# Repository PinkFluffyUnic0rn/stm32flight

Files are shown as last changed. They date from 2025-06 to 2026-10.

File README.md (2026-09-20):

STM32 Flight controller
=========================

DIY quadcopter flight controller from scratch, two boards and software.

[Project structure](https://github.com/PinkFluffyUnic0rn/stm32flight/wiki/Project-structure) 
is described on wiki page.

Software
=======

Software part implements all basic quadcopter flight control features.
Configuration commands and settings are on
[wiki page](https://github.com/PinkFluffyUnic0rn/stm32flight/wiki/FC-configuration-commands-and-settings).

* Rotation speed stabilization using gyroscope readings.
* Attitude stabilization using accelerometer/gyroscope readings.
* Yaw stabilization using gyroscope readings.
* Yaw stabilization using magnetometer/gyroscope readings.
* Acceleration stabilization using accelerometer readings.
* Altitude stabilization using barometer/accelerometer readings.
* Position stabilization using GNSS/accelerometer/magnetometer readings.
* Configuration through Wi-Fi.
* Dshot-300 and Dshot-600 ESC control protocols.
* IRC Tramp VTX control.
* OSD for digital VTX through MSP.
* Telemetry and control through eLRS.
* Terminal configuration tool.
* Qt5 based GUI configuration tool for desktop and android.

STM32H723 based board
=======
[Schematic](https://github.com/PinkFluffyUnic0rn/stm32flight/blob/main/pcb/H7/schematic.pdf)

 * MCU: STM32H723VGT6
 * Crystall oscillator: 20 Mhz
 * DC-DC converter for control board: TPS5430
 * Control board voltage regulator: LDL1117S33R
 * Accelerometer/Gyroscope: ICM-42688-P
 * Barometer: DPS368
 * Magnetometer: LIS3MDL
 * External magnetometer: MMC5983MA
 * Flight log storage: W25Q
 * GNSS module: M10
 * Remote control: ERLS CRSF receiver
 * Telemetry/debug/config: ESP8285

STM32F405 based board
=======
 * MCU: STM32F405RGT6
 * Crystall oscillator: 20 Mhz
 * DC-DC converter for control board: TPS5430 (external)
 * Control board voltage regulator: LDL1117S33R-3.3
 * Accelerometer/Gyroscope: ICM-42688-P
 * Barometer: DPS368
 * Magnetometer: QMC5883L
 * Flight log storage: W25Q
 * GNSS module: M10
 * Remote control: ERLS CRSF receiver
 * Telemetry/debug/config: ESP8285

The quadcopter used for testing
==========
 * Motors: 1404, 3800 kV
 * Props: 3030
 * Battery: 14.8v (4s), 1300 mAh, 120c
 * Frame: carbon fiber
 * Canopy, VTX mount: 3d printed PLA
 * Landing pads: EVA foam

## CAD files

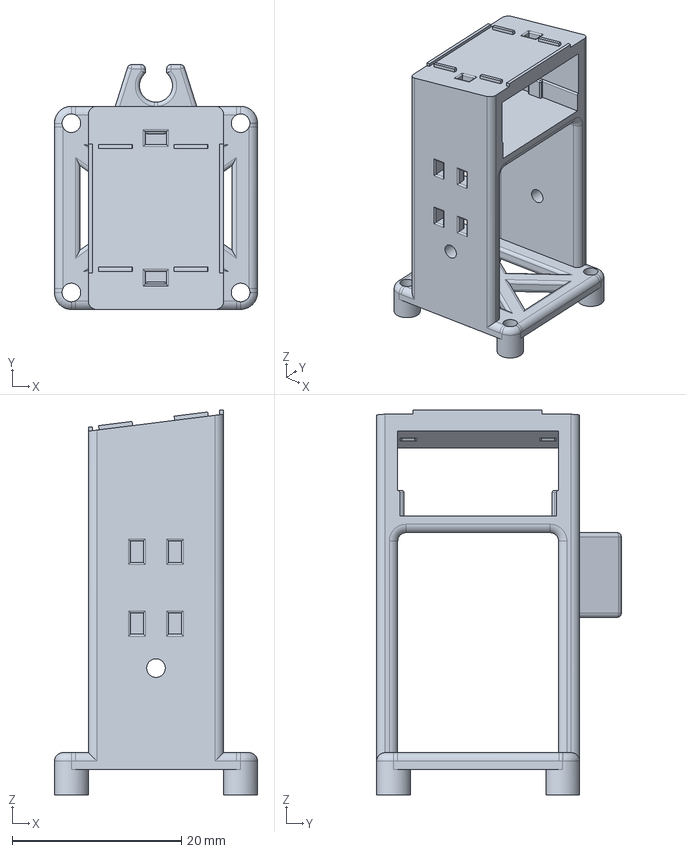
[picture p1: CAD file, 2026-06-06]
cad/canopy.FCStd
24.0 x 28.9 x 45.5 mm

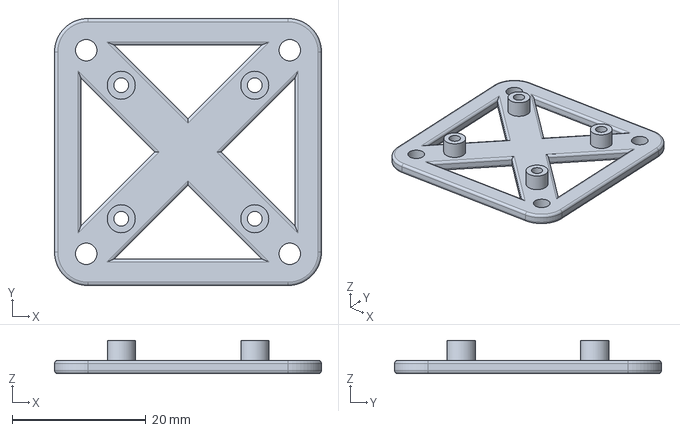
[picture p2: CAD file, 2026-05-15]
cad/vtx_mount.FCStd
40.0 x 40.0 x 5.00 mm

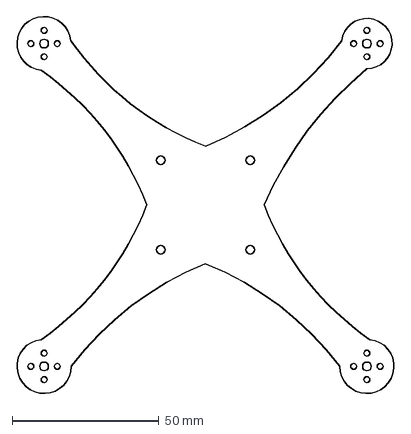
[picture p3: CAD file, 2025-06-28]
cad/frame.dxf
129.1 x 128.8 mm

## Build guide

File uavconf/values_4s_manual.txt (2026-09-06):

adj acc x 0
adj acc y 0
adj acc z 0
adj acc xtscale 0
adj acc ytscale 0
adj acc ztscale 0.00058
adj althold coefa 3.484
adj althold coefb 0
adj althold coefc 0.15
adj althold hover 0.287
adj althold tiltcoefmax 0.25
adj pitch 0.01
adj roll 0
adj yaw 0
adj bat scale 1
adj curr offset -17
adj curr scale 412.5
adj gyro x 1.445184
adj gyro y 0.595486
adj gyro z 0.414855
adj mag x0 0.173815
adj mag y0 -0.076065
adj mag z0 -0.041577
adj mag decl 0.322
adj mag xscale 0.960479
adj mag yscale 0.957427
adj mag zscale 1
adj mag xthscale 0
adj mag ythscale 0
adj mag zthscale 0
adj pitchthrust 0
adj rollthrust 0
adj thrust 1.6
ctrl accel 0.5
ctrl altmax 4
ctrl pitch 0.25
ctrl roll 0.25
ctrl thrust 0.9
ctrl climbrate 1.5
ctrl spitch 1
ctrl spos 2
ctrl sroll 1
ctrl sspeed 4
ctrl syaw 1.5
irc frequency 5865
irc power 25
compl altitude 1
compl attitude 1
compl climbrate 1
compl pos 1
compl speed 1
compl yaw 1
feature matrixatt 1
feature notchen 0
lpf vaccel 1
lpf accel 100
lpf d 100
lpf gyro 100
lpf mag 50
notch gyrovbat 17
notch gyrofrmax 2038
notch gyrofrmin 220
log freq 128
log recsize 8
log record 0 none
log record 1 none
log record 10 none
log record 2 none
log record 3 none
log record 4 none
log record 5 none
log record 6 none
log record 7 none
log record 8 none
log record 9 none
log record 11 none
log record 12 none
log record 13 none
log record 14 none
log record 15 none
log record 16 none
log record 17 none
log record 18 none
log record 19 none
log record 20 none
log record 21 none
log record 22 none
log record 23 none
log record 24 none
log record 25 none
log record 26 none
log record 27 none
log record 28 none
log record 29 none
log record 30 none
log record 31 none
motor lb 1
motor lt 0
motor rb 3
motor rt 2
pid altitude d 0
pid altitude i 0
pid altitude p 1.7
pid tilt d 0
pid tilt i 0
pid tilt p 9
pid climbrate d 0
pid climbrate i 0
pid climbrate p 0.6
pid feature altclamp 1.5
pid feature attimax 0.1
pid feature thrimax 0.1
pid feature iscaling 0.51
pid feature yawclamp 0.125
pid stilt d 0.001667
pid stilt i 8.640009
pid stilt p 0.24
pid throttle d 0
pid throttle i 3
pid throttle p 3
pid syaw d 0
pid syaw i 0
pid syaw p 1.5
pid yaw d 0
pid yaw i 0
pid yaw p 1.5
pid pos d 0
pid pos i 0
pid pos p 1
pid speed d 0
pid speed i 0
pid speed p 5

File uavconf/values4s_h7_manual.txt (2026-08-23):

adj acc x 0
adj acc y 0
adj acc z 0
adj acc xtscale 0
adj acc ytscale 0
adj acc ztscale 0.00058
adj althold coefa 0
adj althold coefb 0
adj althold coefc 0
adj althold hover 0.64
adj althold tiltcoefmax 0.25
adj pitch 0.01
adj roll 0
adj yaw 0
adj bat scale 1
adj curr offset -17
adj curr scale 412.5
adj gyro x 0.945184
adj gyro y 0.795486
adj gyro z 0.414855
adj mag x0 0.077877
adj mag y0 -0.055068
adj mag z0 0.047812
adj mag decl 0.322
adj mag xscale 0.965043
adj mag yscale 0.975738
adj mag zscale 1
adj mag xthscale 0
adj mag ythscale 0
adj mag zthscale 0
adj pitchthrust 0
adj rollthrust 0
adj thrust 1.6
ctrl accel 0.5
ctrl altmax 4
ctrl pitch 0.25
ctrl roll 0.25
ctrl thrust 0.9
ctrl climbrate 1.5
ctrl spitch 1
ctrl spos 2
ctrl sroll 1
ctrl sspeed 4
ctrl syaw 1.5
irc frequency 5865
irc power 25
compl altitude 1
compl attitude 5
compl climbrate 1
compl pos 1
compl speed 1
compl yaw 1
feature matrixatt 1
feature notchen 0
lpf vaccel 0.636
lpf accel 100
lpf d 100
lpf gyro 100
lpf mag 15
notch gyrovbat 7.2
notch gyrofrmax 358
notch gyrofrmin 170
log freq 4000
log recsize 8
log record 0 none
log record 1 none
log record 10 none
log record 2 none
log record 3 none
log record 4 none
log record 5 none
log record 6 none
log record 7 none
log record 8 none
log record 9 none
log record 11 none
log record 12 none
log record 13 none
log record 14 none
log record 15 none
log record 16 none
log record 17 none
log record 18 none
log record 19 none
log record 20 none
log record 21 none
log record 22 none
log record 23 none
log record 24 none
log record 25 none
log record 26 none
log record 27 none
log record 28 none
log record 29 none
log record 30 none
log record 31 none
motor lb 1
motor lt 0
motor rb 3
motor rt 2
pid altitude d 0
pid altitude i 0
pid altitude p 1.7
pid tilt d 0
pid tilt i 0
pid tilt p 9
pid climbrate d 0
pid climbrate i 0
pid climbrate p 0.6
pid feature attimax 0.1
pid feature thrimax 0.1
pid feature iscaling 0.51
pid stilt d 0.003333
pid stilt i 17.280017
pid stilt p 0.48
pid throttle d 0
pid throttle i 6.5
pid throttle p 6.5
pid syaw d 0
pid syaw i 0
pid syaw p 3
pid yaw d 0
pid yaw i 0
pid yaw p 1.5
pid pos d 0
pid pos i 0
pid pos p 0.1
pid speed d 0
pid speed i 0
pid speed p 0.1

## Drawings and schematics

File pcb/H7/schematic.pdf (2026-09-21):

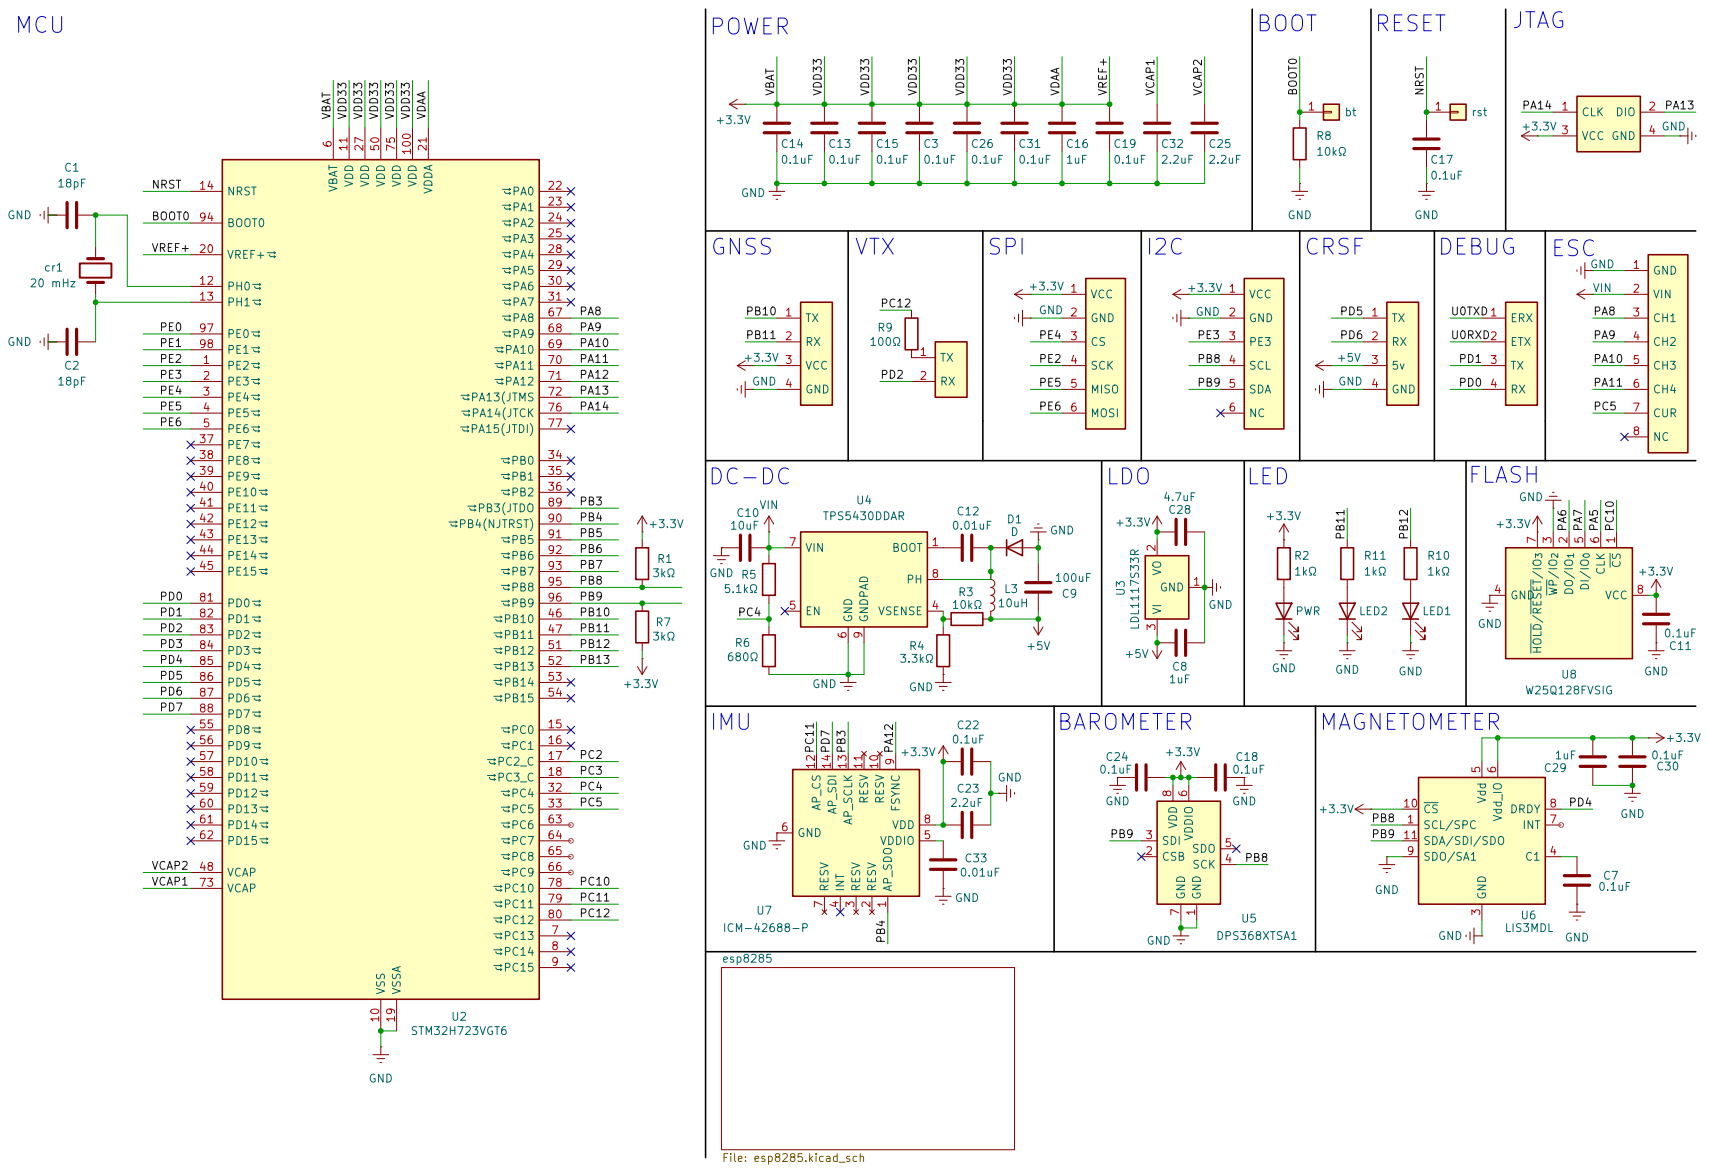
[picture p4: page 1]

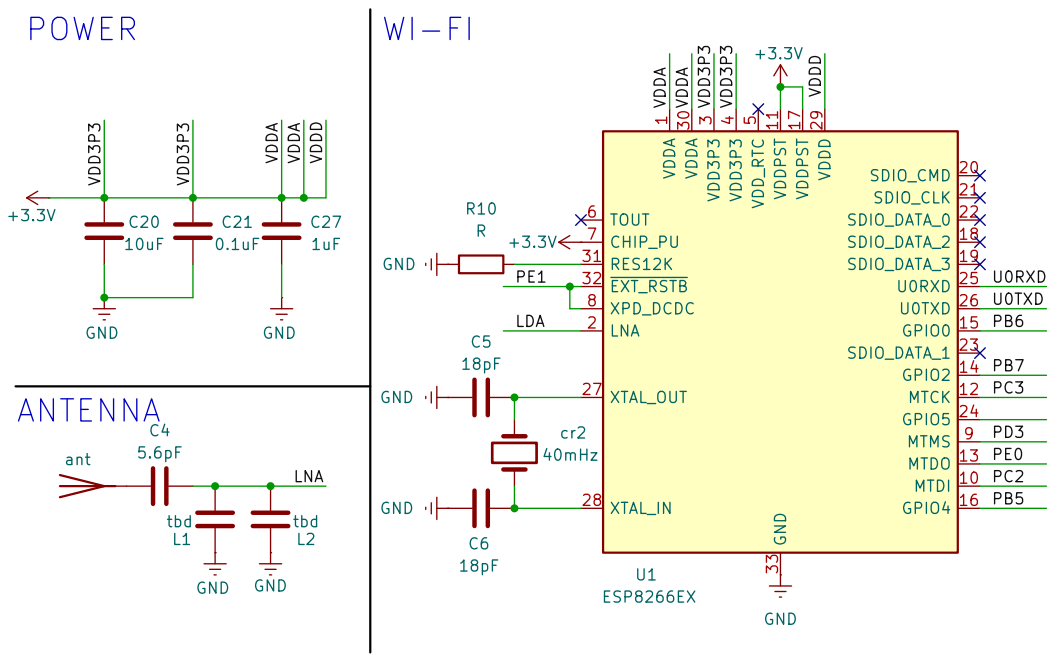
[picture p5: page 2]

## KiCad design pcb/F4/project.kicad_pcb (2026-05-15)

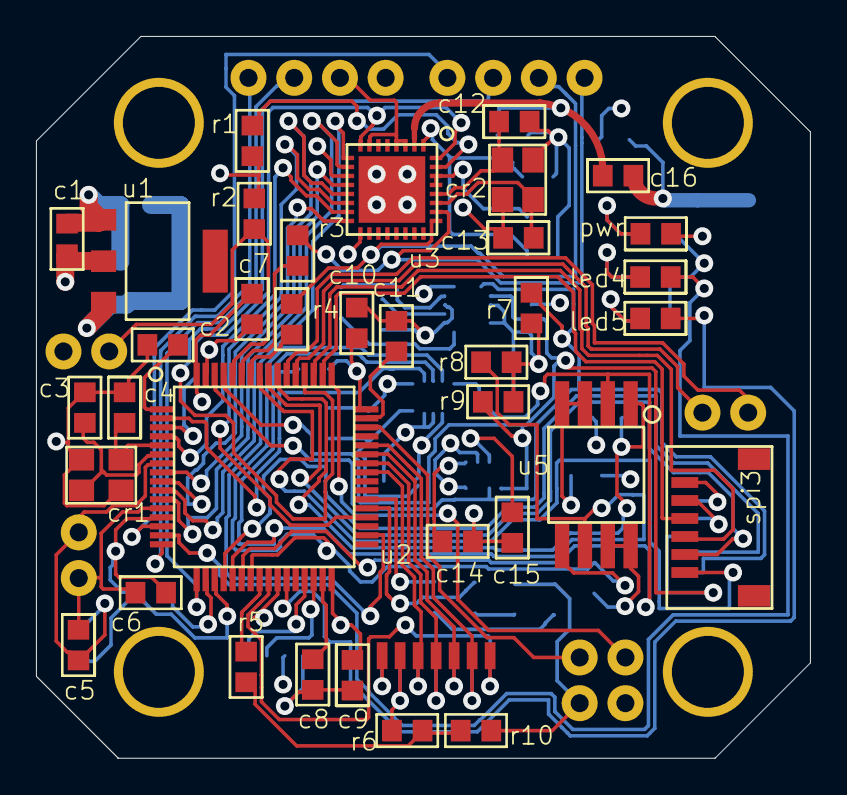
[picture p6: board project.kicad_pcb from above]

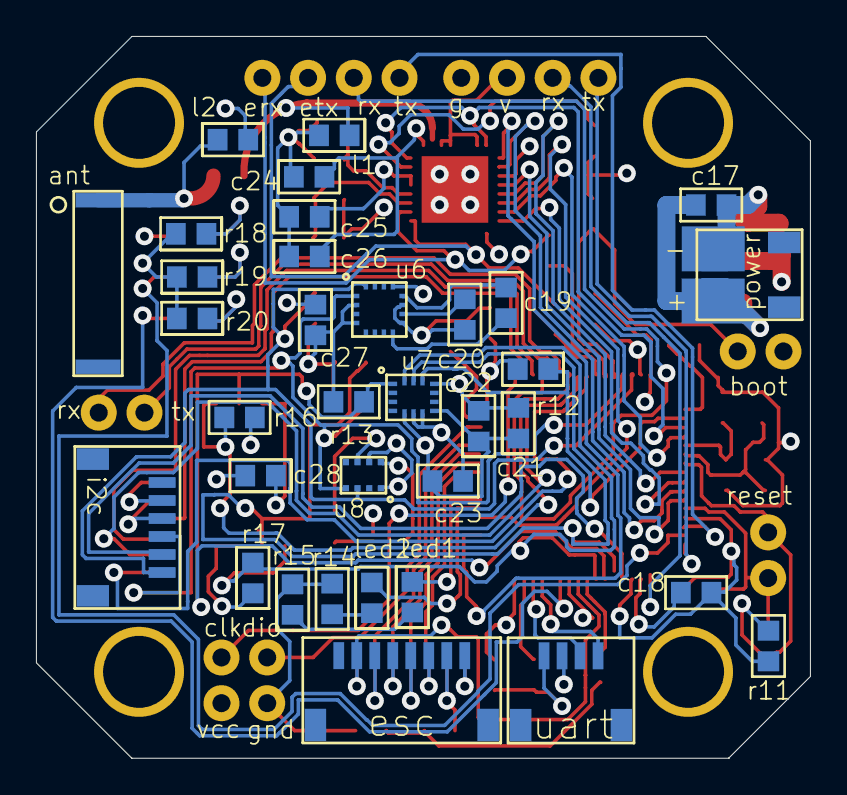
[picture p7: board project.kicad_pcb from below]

Board: 4 copper layers, 43.0 x 40.1 mm, 70 parts (34 on the bottom side), 45 nets.

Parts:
ant: Comment; rainsun antenna
c1: Comment; PCBComponent_1
c2, c3, c4, c5, c6, c7, c8, c9, c10, c11, c12, c13, c14, c15, c16, c17, c18, c19, c20, c21, c22, c23, c24, c25, c26, c27, c28: Comment; 0603
cr1, cr2: Comment; smd_crystall
esc: Comment; SH1.0-8
i2c: Comment; SH1.0-6
l1, l2: Comment; 0603
led1, led2, led4, led5: Comment; 0603
power: Comment; sh1.0-2
pwr: Comment; 0603
r1, r2, r3, r4, r5, r6, r7, r8, r9, r10, r11, r12, r13, r14, r15, r16, r17, r18, r19, r20: Comment; 0603
spi3: Comment; SH1.0-6
u1: Comment; ams1117
u2: Comment; lqfp64
u3: Comment; esp8285
u5: Comment; w25q
u6: Comment; qmc5883l
u7: Comment; icm42688
u8: Comment; DPS368
uart: Comment; sh1.0-4

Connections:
ant: ant.6, c16.1, l2.1
antcap: c16.1, l1.1, u3.4
boot: r2.1, u2.1
ch1: esc.1, u2.1
ch2: esc.1, u2.1
ch3: esc.1, u2.1
ch4: esc.1, u2.1
ch5: spi3.1, u2.1
ch6: spi3.1, u2.1
cs1: r12.1, u2.1, u7.1
cs2: r16.1, u2.1, u5.1
cs4: u2.1, u3.4
current: esc.1, u2.1
esp_rx: r3.1, u3.4
esp_tx: r4.1, u3.4
espboot: u2.1, u3.4
ext_rstb: u2.1, u3.4
exti1: u2.1, u3.4
gnd: c1.1, c2.1, c3.1, c4.1, c5.1, c6.1, c7.1, c8.1, c9.1, c10.1, c11.1, c12.1, c13.1, c14.1, c15.1, c17.1, c18.1, c20.1, c21.1, c22.1, c23.1, c24.1, c25.1, c26.1, c27.1, c28.1, cr1.3, cr2.3, esc.1, i2c.1, l1.1, l2.1, power.1, r1.1, r2.1, r10.1, r14.1, r15.1, r18.1, r19.1, r20.1, spi3.1, u1.1, u2.1, u5.1, u6.1, u7.1, u8.1, uart.1
led1: led2.1, u2.1
led1r: led2.1, r14.1
led2: led1.1, u2.1
led2r: led1.1, r15.1
led3r: pwr.1, r18.1
led4: led4.1, u2.1
led4r: led4.1, r19.1
led5: led5.1, u2.1
led5r: led5.1, r20.1
miso: r13.1, u2.1, u5.1, u7.1
miso2: u2.1, u3.4
mosi: r17.1, u2.1, u5.1, u7.1
mosi2: u2.1, u3.4
nrst: c5.1, r11.1, u2.1
osc_in: c4.1, cr1.3, u2.1
osc_out: c3.1, cr1.3, u2.1
pa4: i2c.1, u2.1
pa15: spi3.1, u2.1
pb15: u2.1, u3.4
pc10: spi3.1, u2.1
qmc_c1: c20.1, u6.1
qmc_setc: c19.1, u6.1
qmc_setp: c19.1, u6.1
res12k: r1.1, u3.4
rx1: r3.1, u2.1
rx3: u2.1, uart.1
sck: r8.1, u2.1, u5.1, u7.1
sck2: u2.1, u3.4
scl: i2c.1, r9.1, u2.1, u6.1, u8.1
sda: i2c.1, r7.1, u2.1, u6.1, u8.1
tx1: r4.1, u2.1
tx3: u2.1, uart.1
v2_1: r5.1, r6.1, r10.1
v2_2: r5.1, u2.1
vbat: c2.1, u2.1
vcap1: c8.1, u2.1
vcap2: c11.1, u2.1
vcc: c1.1, c6.1, c7.1, c9.1, c10.1, c14.1, c15.1, c18.1, c21.1, c22.1, c23.1, c24.1, c25.1, c26.1, c27.1, c28.1, i2c.1, pwr.1, r7.1, r8.1, r9.1, r11.1, r12.1, r13.1, r16.1, r17.1, spi3.1, u1.1, u2.1, u3.4, u5.1, u6.1, u7.1, u8.1, uart.1
vesc: esc.1, r6.1
vin: c17.1, power.1, u1.1
xtal_in: c12.1, cr2.3, u3.4
xtal_out: c13.1, cr2.3, u3.4

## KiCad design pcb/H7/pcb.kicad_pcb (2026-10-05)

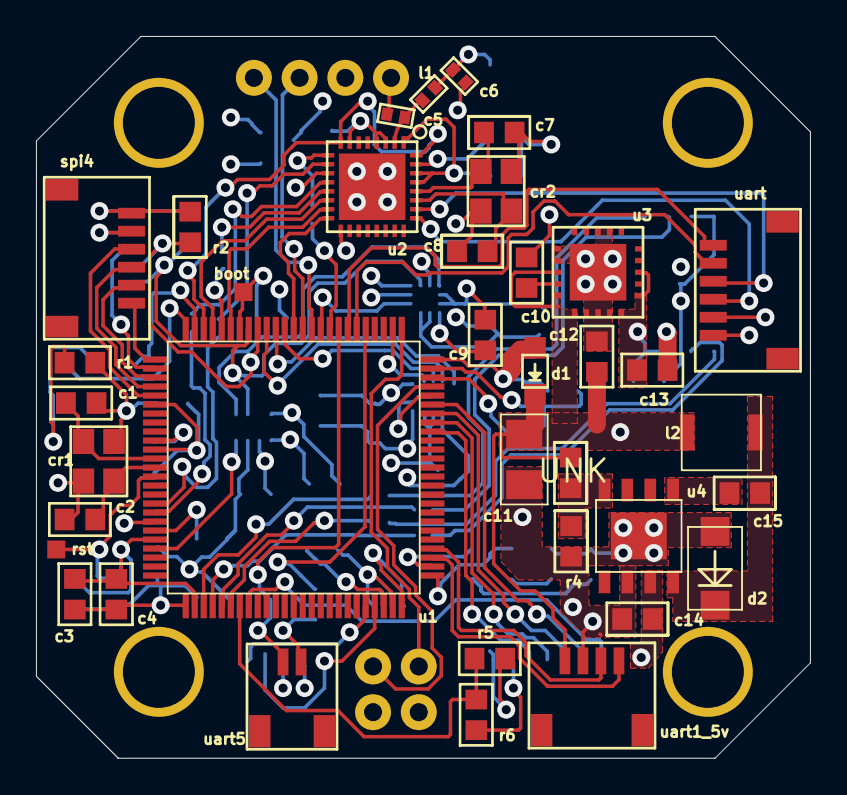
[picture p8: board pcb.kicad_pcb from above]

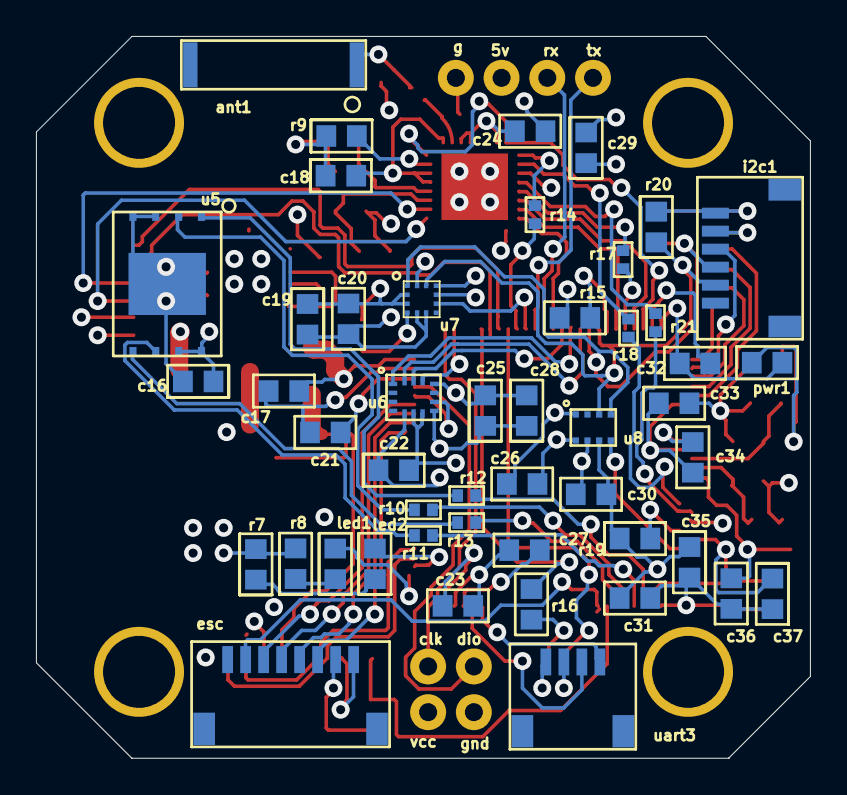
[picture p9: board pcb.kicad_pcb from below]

Board: 4 copper layers, 43.0 x 40.1 mm, 83 parts (48 on the bottom side), 59 nets.

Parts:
UNK: 10 kOhm; 0603
ant1: AN9520; rainsun antenna
c1, c2, c7, c8: 18 pF; 0603
c3, c10, c18, c20, c35: 1 uF; 0603
c4, c9, c16, c17, c19, c23, c24, c25, c26, c30, c31, c32, c33, c34, c36, c37: 0.1 uF; 0603
c5, c6: tbd; 0402
c11: 100 uF; 1206
c12, c14, c29: 10 uF; 0603
c13: 47 uF; 0603
c15, c22: 0.01 uF; 0603
c21, c27, c28: 2.2 uF; 0603
cr1: 20 Mhz; smd_crystall
cr2: 40 Mhz; smd_crystall
d1: Comment; SOD-323
d2: SS34
esc: JST SH-8; SH1.0-8
i2c1: JST SH-6; SH1.0-6
l1: tdb; 0402
l2: 10 uH; inductor
led1: blue LED; 0603
led2: orange LED; 0603
pwr1: green LED; 0603
r1, r7, r8: 1 kOhm; 0603
r2, r20: 3 kOhm; 0603
r4: 3.3 kOhm; 0603
r5: 680 Ohm; 0603
r6: 5.1 kOhm; 0603
r9: 12 kOhm; 0603
r10, r11, r12, r13, r14, r17, r18, r21: 33 Ohm; 0402
r15: 10 kOhm; 0603
r16: 100 Ohm; 0603
r19: 47 Ohm; 0603
spi4: JST SH-6; SH1.0-6
u1: STMH723VGT6; lqfp100
u2: ESP8285; esp8285
u3: TPS7A4700; TPS7A470
u4: TPS5430DDAR; tps5430
u5: Comment; W25N
u6: ICM-42688-P; icm42688
u7: LIS3MDLTR; lis3mdl
u8: DPS368XTSA1; DPS368
uart: JST SH-6; SH1.0-6
uart1_5v, uart3: JST SH-4; sh1.0-4
uart5: JST SH-2; sh1.0-2

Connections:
ant: ant1.6, c6.1, l1.1
antcap: c5.1, l1.1, u2.4
boot: r15.1, u1.1
ch1: esc.1, u1.1
ch2: esc.1, u1.1
ch3: esc.1, u1.1
ch4: esc.1, u1.1
current: esc.1, u1.1
dcdc_boot: c15.1, u4.9
drdy: u1.1, u7.6
esp_rx: u2.4, uart.1
esp_tx: u2.4, uart.1
espboot: u1.1, u2.4
ext_rstb: u1.1, u2.4
exti1: u1.1, u2.4
fsync: u1.1, u6.1
gnd: c1.1, c2.1, c3.1, c4.1, c5.1, c6.1, c7.1, c8.1, c9.1, c10.1, c11.10, c12.1, c13.1, c14.1, c16.1, c17.1, c18.1, c19.1, c20.1, c21.1, c22.1, c23.1, c24.1, c25.1, c26.1, c27.1, c28.1, c29.1, c30.1, c31.1, c32.1, c33.1, c34.1, c35.1, c36.1, c37.1, cr1.3, cr2.3, d2.8, esc.1, i2c1.1, r1.1, r4.1, r5.1, r7.1, r8.1, r9.1, r15.1, spi4.1, u1.1, u3.9, u3.10, u4.9, u5.11, u5.12, u6.1, u7.6, u8.1, uart.1, uart1_5v.1, uart3.1
led1: led1.1, u1.1
led1r: led1.1, r8.1
led2: led2.1, u1.1
led2r: led2.1, r7.1
lis_c1: c9.1, u7.6
loop: c15.1, d2.8, l2.7, u4.9
miso1_1: r10.1, u1.1
miso1_2: r10.1, u5.12
miso2_1: r18.1, u1.1
miso2_2: r18.1, u2.4
miso3: u1.1, u6.1
miso4: spi4.1, u1.1
mosi1_1: r13.1, u1.1
mosi1_2: r13.1, u5.12
mosi2_1: r21.1, u1.1
mosi2_2: r21.1, u2.4
mosi3: u1.1, u6.1
mosi4: spi4.1, u1.1
nr: c10.1, u3.9
nrst: c36.1, u1.1
nss1_1: r12.1, u1.1
nss1_2: r12.1, u5.12
nss2_1: r17.1, u1.1
nss2_2: r17.1, u2.4
nss3: u1.1, u6.1
nss4: spi4.1, u1.1
osc_in: c1.1, cr1.3, u1.1
osc_out: c2.1, cr1.3, u1.1
pe0: u1.1, u2.4
pe3: i2c1.1, u1.1
pwrled: pwr1.1, r1.1
res12k: r9.1, u2.4
rx1: u1.1, uart1_5v.1
rx3: u1.1, uart3.1
rx4: u1.1, uart.1
rx5: u1.1, uart5.1
sck1_1: r11.1, u1.1
sck1_2: r11.1, u5.12
sck2_1: r14.1, u1.1
sck2_2: r14.1, u2.4
sck3: u1.1, u6.1
sck4: spi4.1, u1.1
scl: i2c1.1, r2.1, u1.1, u7.6, u8.1
sda: i2c1.1, r20.1, u1.1, u7.6, u8.1
sdo: u1.1, u8.1
sence: UNK.1, r4.1, u4.9
tx1: u1.1, uart1_5v.1
tx3: u1.1, uart3.1
tx4: u1.1, uart.1
tx5_1: r16.1, u1.1
tx5_2: r16.1, uart5.1
v5: UNK.1, c11.10, c12.1, d1.4, l2.7, u3.9, uart1_5v.1
v_bat: r5.1, r6.1, u1.1
vcap1: c21.1, u1.1
vcap2: c27.1, u1.1
vcc: c3.1, c4.1, c13.1, c16.1, c17.1, c18.1, c19.1, c20.1, c22.1, c23.1, c24.1, c25.1, c26.1, c28.1, c29.1, c30.1, c31.1, c32.1, c33.1, c34.1, c35.1, c37.1, d1.4, i2c1.1, pwr1.1, r2.1, r19.1, r20.1, spi4.1, u1.1, u2.4, u3.9, u5.12, u6.1, u7.6, u8.1, uart.1, uart3.1
vin: c14.1, esc.1, r6.1, u4.9
vref+: r19.1, u1.1
xtal_in: c7.1, cr2.3, u2.4
xtal_out: c8.1, cr2.3, u2.4

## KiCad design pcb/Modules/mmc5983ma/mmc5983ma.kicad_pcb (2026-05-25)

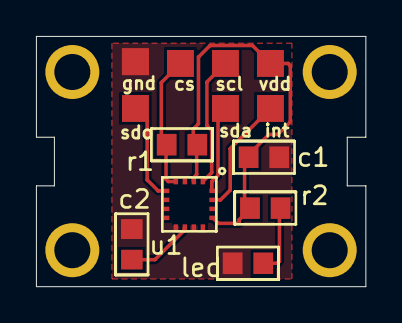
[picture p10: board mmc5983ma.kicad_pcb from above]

Board: 2 copper layers, 18.3 x 13.9 mm, 6 parts (0 on the bottom side), 5 nets.

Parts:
c1, c2: Comment; 0603
led: Comment; 0603
r1, r2: Comment; 0603
u1: Comment; qmc5883l

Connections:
cap: c2.1, u1.1
cs: r1.1, u1.1
gnd: c1.1, c2.1, led.1, u1.1
led: led.1, r2.1
vcc: c1.1, r1.1, r2.1, u1.1

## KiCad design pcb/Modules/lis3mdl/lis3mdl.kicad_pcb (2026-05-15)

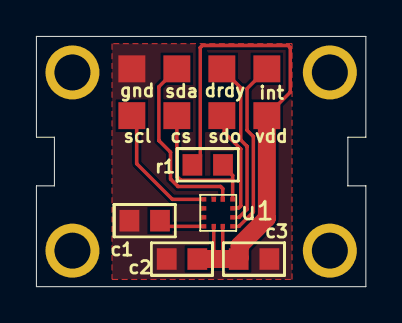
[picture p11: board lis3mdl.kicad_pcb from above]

Board: 2 copper layers, 18.3 x 13.9 mm, 5 parts (0 on the bottom side), 4 nets.

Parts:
c1, c2, c3: Comment; 0603
r1: Comment; 0603
u1: Comment; lis3mdl

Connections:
c1: c1.1, u1.6
cs: r1.1, u1.6
gnd: c1.1, c2.1, c3.1, u1.6
vdd: c2.1, c3.1, r1.1, u1.6

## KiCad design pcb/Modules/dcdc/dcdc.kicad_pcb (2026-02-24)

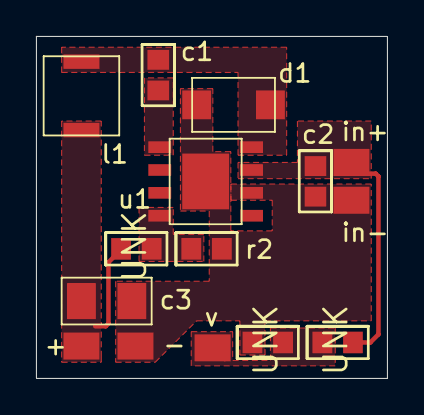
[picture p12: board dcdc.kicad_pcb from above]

Board: 2 copper layers, 19.5 x 19.0 mm, 10 parts (0 on the bottom side), 7 nets.

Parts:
UNK: Comment; 0603
UNK#2, UNK#3: Comment; 0603
c1, c2: Comment; 0603
c3: Comment; 1206
d1: Comment; SS34
l1: Comment; inductor
r2: Comment; 0603
u1: Comment; tps5430

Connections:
boot: c1.1, u1.9
gnd: UNK#3.1, c2.1, c3.10, d1.8, r2.1, u1.9
in: UNK.1, c2.1, u1.9
loop: c1.1, d1.8, l1.7, u1.9
out: UNK#2.1, c3.10, l1.7
sense: UNK#2.1, r2.1, u1.9
v: UNK.1, UNK#3.1

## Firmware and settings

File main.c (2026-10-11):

/**
* @file main.c
* @brief Main file with entry point
*/

#include <math.h>
#include <string.h>
#include <stdio.h>
#include <stdarg.h>
#include <stdlib.h>
#include <ctype.h>

#include "mcudef.h"

#include "periphconf.h"
#include "settings.h"
#include "dsp.h"
#include "log.h"
#include "controlloop.h"
#include "crc.h"
#include "runvals.h"
#include "timev.h"
#include "command.h"
#include "config.h"
#include "util.h"

#include "device.h"
#include "icm42688.h"
#include "dps368.h"
#include "esp8266.h"
#include "qmc5883l.h"
#include "crsf.h"
#include "w25.h"
#include "m10.h"
#include "uartconf.h"
#include "irc.h"
#include "msp.h"
#include "tfluna.h"
#include "dshot.h"

/**
* @brief External interrupt callback. It calls interrupt handlers
	from drivers for devices that use external interrupts.
* @param pin number of pin triggered the callback
* @return none
*/
void HAL_GPIO_EXTI_Callback(uint16_t pin)
{
	if (DEVITENABLED(Dev[DEV_RF].status)) {
		Dev[DEV_RF].interrupt(Dev[DEV_RF].priv, &pin);
	}
}

/**
* @brief UART receive callback. It calls interrupt handlers
	from drivers for devices working through UART.
* @param huart context for UART triggered that callback
* @return none
*/
void HAL_UART_RxCpltCallback(UART_HandleTypeDef *huart)
{
	if (DEVITENABLED(Dev[DEV_GNSS].status))
		Dev[DEV_GNSS].interrupt(Dev[DEV_GNSS].priv, huart);

	if (DEVITENABLED(Dev[DEV_CRSF].status))
		Dev[DEV_CRSF].interrupt(Dev[DEV_CRSF].priv, huart);

	if (DEVITENABLED(Dev[DEV_VTX].status))
		Dev[DEV_VTX].interrupt(Dev[DEV_VTX].priv, huart);

	if (DEVITENABLED(Dev[DEV_UART].status))
		Dev[DEV_UART].interrupt(Dev[DEV_UART].priv, huart);

	if (DEVITENABLED(Dev[DEV_LIDAR].status))
		Dev[DEV_LIDAR].interrupt(Dev[DEV_LIDAR].priv, huart);
}

/**
* @brief SPI transmit callback. It calls interrupt handlers
	from drivers for devices working through SPI.
* @param hspi context for SPI triggered that callback
* @return none
*/
void HAL_SPI_TxCpltCallback(SPI_HandleTypeDef *hspi)
{
	if (DEVITENABLED(Flashdev.status))
		Flashdev.interrupt(Flashdev.priv, hspi);
}

/**
* @brief SPI receive callback. It calls interrupt handlers
	from drivers for devices working through SPI.
* @param hspi context for SPI triggered that callback
* @return none
*/
void HAL_SPI_TxRxCpltCallback(SPI_HandleTypeDef *hspi)
{
	if (DEVITENABLED(Dev[DEV_IMU].status))
		Dev[DEV_IMU].interrupt(Dev[DEV_IMU].priv, hspi);
}

/**
* @brief UART error callback. Calls UART error handlers
	from drivers for devices working through UART.
* @param huart context for UART triggered that callback.
* @return none
*/
void HAL_UART_ErrorCallback(UART_HandleTypeDef *huart)
{
	if (DEVITENABLED(Dev[DEV_CRSF].status))
		Dev[DEV_CRSF].error(Dev[DEV_CRSF].priv, huart);

	if (DEVITENABLED(Dev[DEV_VTX].status))
		Dev[DEV_VTX].error(Dev[DEV_VTX].priv, huart);
}

/**
* @brief Non-maskable interrupt handler.
* @return none
*/
void NMI_Handler(void)
{
	TIM1->CCR1 = TIM1->CCR2 = TIM1->CCR3 = TIM1->CCR4 = 0;

	HAL_GPIO_WritePin(ERROR_GPIO, ERROR_PIN, GPIO_PIN_SET);

	while (1) {}
}

/**
* @brief Hard-fault interrupt handler.
* @return none
*/
void HardFault_Handler(void)
{
	TIM1->CCR1 = TIM1->CCR2 = TIM1->CCR3 = TIM1->CCR4 = 0;

	HAL_GPIO_WritePin(ERROR_GPIO, ERROR_PIN, GPIO_PIN_SET);
	
	while (1) {}
}

/**
* @brief Memory management error interrupt handler.
* @return none
*/
void MemManage_Handler(void)
{
	TIM1->CCR1 = TIM1->CCR2 = TIM1->CCR3 = TIM1->CCR4 = 0;
	
	HAL_GPIO_WritePin(ERROR_GPIO, ERROR_PIN, GPIO_PIN_SET);

	while (1) {}
}

/**
* @brief Bus fault error interrupt handler.
* @return none
*/
void BusFault_Handler(void)
{
	TIM1->CCR1 = TIM1->CCR2 = TIM1->CCR3 = TIM1->CCR4 = 0;
	
	HAL_GPIO_WritePin(ERROR_GPIO, ERROR_PIN, GPIO_PIN_SET);
	
	while (1) {}
}

/**
* @brief Usage fault error interrupt handler.
* @return none
*/
void UsageFault_Handler(void)
{
	TIM1->CCR1 = TIM1->CCR2 = TIM1->CCR3 = TIM1->CCR4 = 0;
	
	HAL_GPIO_WritePin(ERROR_GPIO, ERROR_PIN, GPIO_PIN_SET);

	while (1) {}
}

/**
* @brief HAL error handler.
* @return none
*/
void error_handler(void)
{
	TIM1->CCR1 = TIM1->CCR2 = TIM1->CCR3 = TIM1->CCR4 = 0;

	HAL_GPIO_WritePin(ERROR_GPIO, ERROR_PIN, GPIO_PIN_SET);

	__disable_irq();
	while (1) {}
}

/**
* @brief Get ADC sampled value.
* @param hadc ADC handle
* @param buf write buffer for DMA
* @return samlped value
*/
double adcvalue(ADC_HandleTypeDef *hadc, volatile uint16_t *buf)
{
	uint32_t v;
	int t;

	t = 0;
	while ((HAL_ADC_GetState(hadc) & HAL_ADC_STATE_REG_BUSY) != 0
			&& t < 100000) {
		udelay(10);
		t += 10;
	}

	v = *buf;

	HAL_ADC_Start_DMA(hadc, (uint32_t *) buf, 1);

	return v;
}

/**
* @brief Get battery voltage from ADC.
* @return battery voltage
*/
double batteryvoltage()
{
	ADC_HandleTypeDef *hadc;
	static volatile uint16_t buf = 0;

	hadc = pconf_batteryhadc;

	return (adcvalue(hadc, &buf)
		/ (double) 0xfff * BAT_SCALE * St.adj.batsc);
}

/**
* @brief Get ESC current from ADC.
* @return battery current in amperes
*/
double esccurrent()
{
	ADC_HandleTypeDef *hadc;
	static volatile uint16_t buf = 0;
	
	hadc = pconf_currenthadc;

	return (adcvalue(hadc, &buf)
		/ (double) 0xfff * St.adj.current.scale
		+ St.adj.current.offset);

}

/**
* @brief Get readings from IMU. Callback for TEV_IMU periodic event.
* @param ms microsecond passed from last callback invocation
* @return always 0
*/
int imuupdate(int ms)
{
	double gx, gy, gz;
	double vcoef, thr, frq;

	// if IMU isn't initilized, return
	if (Dev[DEV_IMU].status != DEVSTATUS_INIT)
		return 0;

	// get accelerometer and gyroscope readings
	Dev[DEV_IMU].read(Dev[DEV_IMU].priv, &Imudata,
		sizeof(struct imu_data));

	// apply accelerometer offsets
	Imudata.afx += (Imudata.ft - 25.0) * St.adj.acctsc.x;
	Imudata.afy += (Imudata.ft - 25.0) * St.adj.acctsc.y;
	Imudata.afz += (Imudata.ft - 25.0) * St.adj.acctsc.z;

	Imudata.afx += St.adj.acc0.x;
	Imudata.afy += St.adj.acc0.y;
	Imudata.afz += St.adj.acc0.z;

	// apply gyroscope offsets
	Imudata.gfx += St.adj.gyro0.x;
	Imudata.gfy += St.adj.gyro0.y;
	Imudata.gfz += St.adj.gyro0.z;

	// write accelerometer and gyroscope values into log
	writelog(LOG_ACC_X, Imudata.afx);
	writelog(LOG_ACC_Y, Imudata.afy);
	writelog(LOG_ACC_Z, Imudata.afz);
	writelog(LOG_GYRO_X, Imudata.gfx);
	writelog(LOG_GYRO_Y, Imudata.gfy);
	writelog(LOG_GYRO_Z, Imudata.gfz);

	if (St.feature.notchen != 0) {
		// calculate frequency for gyroscope notch filter	
		vcoef = dsp_getlpf(Lpf + LPF_BAT) / St.notch.gyrovbat;
		thr = dsp_getlpf(Lpf + LPF_AVGTHR) * vcoef * vcoef;

		frq = St.notch.gyrofrmin + thr * thr
			* (St.notch.gyrofrmax - St.notch.gyrofrmin);
		
		// update notch filter's coefficients	
		dsp_setnotch2(&Flt, frq, 300.0, PID_FREQ, 0);
		
		// update notch filter
		dsp_updatefilterv(&Flt,
			Imudata.gfx, Imudata.gfy, Imudata.gfz,
			&gx, &gy, &gz);
	}
	else {
		gx = Imudata.gfx;
		gy = Imudata.gfy;
		gz = Imudata.gfz;
	}

	// update accelerometer values
	dsp_updatelpf(Lpf + LPF_ACCX, Imudata.afx);
	dsp_updatelpf(Lpf + LPF_ACCY, Imudata.afy);
	dsp_updatelpf(Lpf + LPF_ACCZ, Imudata.afz);

	// update gyroscope values
	dsp_updatelpf(Lpf + LPF_GYROX, gx);
	dsp_updatelpf(Lpf + LPF_GYROY, gy);
	dsp_updatelpf(Lpf + LPF_GYROZ, gz);

	// update accelerometer temperature
	dsp_updatelpf(Lpf + LPF_IMUTEMP, Imudata.ft);

	return 0;
}

/**
* @brief Postion estimation and stabilization loop. Callback for
* 	TEV_PID periodic event. It is the place where is almost all work
* 	happening.
* @param ms microsecond passed from last callback invocation
* @return always 0
*/
int stabilize(int ms)
{
	struct corvals cor;
	double dt;
	
	// debug pin switching
	HAL_GPIO_WritePin(debuggpio, debugpin,
		!(HAL_GPIO_ReadPin(debuggpio, debugpin)));

	// emergency disarm happened
	if (Emergencydisarm) {
		setthrust(Dev + DEV_DSHOT, 0.0, 0.0, 0.0, 0.0);
		En = 0.0;
	}

	// get time passed from last invocation of this calback function
	dt = ms / (double) TICKSPERSEC;

	// divide-by-zero protection
	dt = (dt < 0.000001) ? 0.000001 : dt;

	// update battery voltage
	writelog(LOG_BAT, dsp_getlpf(Lpf + LPF_BAT));

	// toggle arming indication led
	HAL_GPIO_WritePin(armgpio, armpin,
		(En > 0.5) ? GPIO_PIN_SET : GPIO_PIN_RESET);

	// update acceleration, speed, position,
	// rotation speed, and rotation for all 3 axes
	updateposition(dt);

	// get correction values for roll, pitch, yaw and thrust
	updatecorrection(dt, &cor);

	// apply thrust to motors
	applythrust(&cor);

	// update loops counter
	++Loops;

	return 0;
}

/**
* @brief Check if ERLS connection is alive, disarm if not. Callback
	for TEV_CHECK periodic event.
* @param ms microsecond passed from last callback invocation
* @return always 0
*/
int checkconnection(int ms)
{
	// decrease ERLS timeout counter
	if (Elrstimeout != 0)
		--Elrstimeout;

	// if timeout conter reached 0 and no ERLS
	// packet came, disarm immediately
	if (Elrstimeout <= 0) {
		Emergencydisarm = 1;
		setthrust(Dev + DEV_DSHOT, 0.0, 0.0, 0.0, 0.0);
		En = 0.0;
	}

	// since it runs every 1 second update loop counter here too
	Loopscount = Loops;
	Loops = 0;

	return 0;
}

/**
* @brief Get readings from barometer. Callback for
	TEV_BARO periodic event.
* @param ms microsecond passed from last callback invocation
* @return always 0
*/
int baroupdate(int ms)
{
	// if barometer isn't initilized, return
	if (Dev[DEV_BARO].status != DEVSTATUS_INIT)
		return 0;

	// read barometer values
	Dev[DEV_BARO].read(Dev[DEV_BARO].priv, &Barodata,
		sizeof(struct baro_data));

	// write barometer temperature and altitude values into log
	writelog(LOG_BAR_TEMP, Barodata.tempf);
	writelog(LOG_BAR_ALT, Barodata.altf);

	// update altitude low-pass filter and temperature reading
	dsp_updatelpf(Lpf + LPF_ALT, Barodata.altf);
	dsp_updatelpf(Lpf + LPF_BARTEMP, Barodata.tempf);

	return 0;
}

/**
* @brief Get readings from magnetomer. Callback for TEV_MAG
	periodic event.
* @param ms microsecond passed from last callback invocation
* @return always 0
*/
int magupdate(int ms)
{
	// if magnetometer isn't initilized, return
	if (Dev[DEV_MAG].status != DEVSTATUS_INIT)
		return 0;

	Dev[DEV_MAG].read(Dev[DEV_MAG].priv, &Magdata,
		sizeof(struct mag_data));

	// apply offsets to magnetometer values
	Magdata.fx = St.adj.magsc.x * (Magdata.fx + St.adj.mag0.x);
	Magdata.fy = St.adj.magsc.y * (Magdata.fy + St.adj.mag0.y);
	Magdata.fz = St.adj.magsc.z * (Magdata.fz + St.adj.mag0.z);

	// apply scaling to magnetometer values
	Magdata.fx += St.adj.magthrsc.x * dsp_getlpf(Lpf + LPF_AVGTHR);
	Magdata.fy += St.adj.magthrsc.y * dsp_getlpf(Lpf + LPF_AVGTHR);
	Magdata.fz += St.adj.magthrsc.z * dsp_getlpf(Lpf + LPF_AVGTHR);

	// write magnetometer values into log
	writelog(LOG_MAG_X, Magdata.fx);
	writelog(LOG_MAG_Y, Magdata.fy);
	writelog(LOG_MAG_Z, Magdata.fz);

	// update magnetometer values lpf
	dsp_updatelpf(Lpf + LPF_MAGX, Magdata.fx);
	dsp_updatelpf(Lpf + LPF_MAGY, Magdata.fy);
	dsp_updatelpf(Lpf + LPF_MAGZ, Magdata.fz);

	return 0;
}

/**
* @brief Update log frame. If buffer isn't full, just move
	buffer pointer, otherwise save buffer content into flash and
	set buffer pointer to 0.
* @param ms microsecond passed from last callback invocation
* @return always 0
*/
int logupdate(int ms)
{
	updatelog();

	return 0;
}

/**
* @brief Send telemetry through ELRS.
* @param ms microsecond passed from last callback invocation
* @return always 0
*/
int telesend(int ms)
{
	const char *attmodestr[] = {"ac", "st", "sp", "ps"};
	const char *yawmodestr[] = {"sp", "cs"};
	const char *altmodestr[] = {"tr", "cl", "al"};
	const char *am;

	Tele.bat = dsp_getlpf(Lpf + LPF_BAT);
	Tele.curr = dsp_getlpf(Lpf + LPF_CUR);

	// Determine battery series cells count using it voltage
	// and calculate it's remaining charge in percents
	if (Tele.bat < 6.0)
		Tele.batrem = (Tele.bat - 3.5) / 0.7;
	else if (Tele.bat < 9.0)
		Tele.batrem = (Tele.bat - 7.0) / 1.4;
	else if (Tele.bat < 13.5)
		Tele.batrem = (Tele.bat - 10.5) / 2.1;
	else if (Tele.bat < 18.0)
		Tele.batrem = (Tele.bat - 14) / 2.8;
	else
		Tele.batrem = (Tele.bat - 21) / 3.5;

	Tele.batrem = trimf(100.0 * Tele.batrem, 0.0, 100.0);

	Tele.lat = Gnss.declat;
	Tele.lon = Gnss.declon;
	Tele.speed = dsp_getlpf(Lpf + LPF_SPEED);
	Tele.course = Gnss.course;
	Tele.alt = Gnss.altitude;
	Tele.sats = Gnss.satellites;
	Tele.balt = dsp_getcompl(Cmpl + CMPL_ALT) - Alt0;
	Tele.vspeed = dsp_getcompl(Cmpl + CMPL_CLIMBRATE);
	Tele.roll = dsp_getlpf(Lpf + LPF_ROLL);
	Tele.pitch = dsp_getlpf(Lpf + LPF_PITCH);
	Tele.yaw = dsp_getlpf(Lpf + LPF_YAW);

	// fill flight mode string with arm state and
	// combination of stabilization modes codes
	if (Altmode == ALTMODE_ACCEL)
		am = altmodestr[0];
	else if (Altmode == ALTMODE_SPEED)
		am = altmodestr[1];
	else if (Altmode == ALTMODE_POS)
		am = altmodestr[2];
	else
		am = "---";

	Tele.mode[0] = En > 0.5 ? 'a' : 'n';
	Tele.mode[1] = '|';
	
	if (Gnssmode == GNSSMODE_SPEED)
		memcpy(Tele.mode + 2, attmodestr[2], 2);
	else if (Gnssmode == GNSSMODE_POS)
		memcpy(Tele.mode + 2, attmodestr[3], 2);
	else
		memcpy(Tele.mode + 2, attmodestr[Speedpid ? 0 : 1], 2);
	
	Tele.mode[4] = '|';
	memcpy(Tele.mode + 5, yawmodestr[Yawspeedpid ? 0 : 1], 2);
	Tele.mode[7] = '|';
	memcpy(Tele.mode + 8, am, 2);

	// in case of emergency disarming
	// set flight mode to "stopped"
	if (Emergencydisarm)
		strcpy((char *) Tele.mode, "stopped");

	// perform telemetry write step	on CRSF eLRS
	// reciever to send it back to remote
	Dev[DEV_CRSF].write(Dev[DEV_CRSF].priv, &Tele,
		sizeof(struct crsf_tele));

	Osd.armed = (En > 0.5) ? 1 : 0;
	Osd.attmode = Speedpid ? MSP_ATTMODE_GYRO : MSP_ATTMODE_ACC;
	Osd.yawmode = Yawspeedpid ? MSP_YAWMODE_GYRO : MSP_YAWMODE_MAG;

	if (Altmode == ALTMODE_ACCEL)
		Osd.altmode = MSP_ALTMODE_ACCEL;
	else if (Altmode == ALTMODE_SPEED)
		Osd.altmode = MSP_ALTMODE_SPEED;
	else if (Altmode == ALTMODE_POS)
		Osd.altmode = MSP_ALTMODE_POS;

	if (Gnssmode == GNSSMODE_NONE)
		Osd.gnssmode = MSP_GNSSMODE_NONE;
	else if (Gnssmode == GNSSMODE_SPEED)
		Osd.gnssmode = MSP_GNSSMODE_SPEED;
	else if (Gnssmode == GNSSMODE_POS)
		Osd.gnssmode = MSP_GNSSMODE_POS;

	Osd.bat = Tele.bat;
	Osd.curr = Tele.curr;
	Osd.batrem = Tele.batrem;
	Osd.lat = Tele.lat;
	Osd.lon = Tele.lon;
	Osd.speed = Tele.speed;
	Osd.course = Tele.course;
	Osd.alt = Tele.balt;
	Osd.sats = Tele.sats;
	Osd.vspeed = Tele.vspeed;
	Osd.temp = dsp_getlpf(Lpf + LPF_BARTEMP);
	Osd.roll = Tele.roll;
	Osd.pitch = Tele.pitch;
	Osd.yaw = Tele.yaw;

	// perform OSD draw step on VTX device
	Dev[DEV_VTX].write(Dev[DEV_VTX].priv, &Osd,
		sizeof(struct msp_osd));

	return 0;
}

/**
* @brief Update battery voltage and current.
* @param ms microsecond passed from last callback invocation
* @return always 0
*/
int powercheck(int ms)
{
	dsp_updatelpf(Lpf + LPF_BAT, batteryvoltage());
	dsp_updatelpf(Lpf + LPF_CUR, esccurrent());

	return 0;
}

int initautopilot()
{
	Strun.autopilot.type[0] = AUTOPILOT_START;

	Strun.autopilot.type[1] = AUTOPILOT_TAKEOFF;
	Strun.autopilot.alt[1] = 1.5;

	Strun.autopilot.type[2] = AUTOPILOT_HOVER;
	Strun.autopilot.t[2] = 5.0;

	Strun.autopilot.type[3] = AUTOPILOT_LANDING;

	Strun.autopilot.type[4] = AUTOPILOT_STOP;

	Strun.autopilot.count = 5;

	updateautopilot();

	return 0;
}

/**
* @brief Move to next point in autopilot track.
* @return always 0
*/
int autopilotstep(int *stepped)
{
	Autopilottimer = 0;
	*stepped = 1;
	++Curpoint;

	return 0;
}

/**
* @brief Update control values when moving in autopilot mode.
* @param ms microsecond passed from last callback invocation
* @return always 0
*/
int autopilotupdate(int ms)
{
	static int lidarfixed = 0;
	static int stepped = 0;
	int s;
	struct trackpoint *point;
	double dt;

	dt = ms / (double) TICKSPERSEC;
	
	// divide-by-zero protection
	dt = (dt < 0.000001) ? 0.000001 : dt;

	if (!Autopilot || Pointscount == 0 || Curpoint < 0
			|| Curpoint >= Pointscount) {
		return 0;
	}

	s = 0;
	if (stepped) {
		s = 1;
		stepped = 0;
	}

	point = Points + Curpoint;
	if (point->type == AUTOPILOT_START)
		autopilotstep(&stepped);
	else if (point->type == AUTOPILOT_TAKEOFF) {
		Altref = 0;

		if (dsp_getcompl(Cmpl + CMPL_ALT) - Alt0 > 5.0)
			Thrust = point->takeoff.alt;
		else if (dsp_getcompl(Cmpl + CMPL_ALT) - Alt0 > 1.0)
			Thrust += dt;
		else if (dsp_getcompl(Cmpl + CMPL_ALT) - Alt0 > 0.5)
			Thrust += dt * 0.5;
		else
			Thrust += dt * 0.25;
		
		if (fabs(dsp_getcompl(Cmpl + CMPL_ALT) - Alt0
				- point->takeoff.alt) <= 0.1) {
			Thrust = point->takeoff.alt;
			autopilotstep(&stepped);
		}
	}
	else if (point->type == AUTOPILOT_HOVER) {
		Autopilottimer += dt;

		if (Autopilottimer > point->hover.t)
			autopilotstep(&stepped);
	}
	else if (point->type == AUTOPILOT_FORWARD) {
		double dlat, dlon;

		Gnssmode = GNSSMODE_POS;

		Rolltarget = point->forward.x;
		Pitchtarget = point->forward.y;

		dlat = Pitchtarget - dsp_getcompl(Cmpl + CMPL_LAT);
		dlon = Rolltarget - dsp_getcompl(Cmpl + CMPL_LON);

		if (dlat * dlat + dlon * dlon < 0.25)
			autopilotstep(&stepped);
	}
	else if (point->type == AUTOPILOT_LANDING) {
		double curalt;

		if (s)
			lidarfixed = 0;

		if (Lidardata.isvalid && lidarfixed == 0) {
			Thrust = dsp_getcompl(Cmpl + CMPL_GNDALT);
			lidarfixed = 1;
		}
		else if (Lidardata.isvalid == 0 && lidarfixed) {
			Thrust = dsp_getcompl(Cmpl + CMPL_ALT) - Alt0;
			lidarfixed = 0;
		}

		if (lidarfixed) {
			curalt = dsp_getcompl(Cmpl + CMPL_GNDALT);
			Altref = 1;
		}
		else {
			curalt = dsp_getcompl(Cmpl + CMPL_ALT) - Alt0;
			Altref = 0;
		}

		if (curalt > 5.0)		Thrust -= dt;
		else if (curalt > 2.0)		Thrust -= dt * 0.5;
		else if (curalt > 1.0)		Thrust -= dt * 0.25;
		else				Thrust -= dt * 0.125;
		
		if (curalt <= 0.01 || Thrust < -0.5)
			autopilotstep(&stepped);
	}
	else if (point->type == AUTOPILOT_STOP) {
		Thrust = -1.0;
	}

	return 0;
}
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
int main(void)
{
	// init periphery
	pconf_init(error_handler);
	
	// reading settings from memory current
	// memory slot, which is 0 at start
	readsettings(Curslot);

	// set IRC VTX power and frequency using values from settings
	updatevtx();

	initautopilot();

	// initialize stabilization routine
	setstabilize(1);

	// initilize periodic events
	inittimev(Evs + TEV_IMU, 0, PID_FREQ, imuupdate);
	inittimev(Evs + TEV_LOG, 0, Strun.log.freq,  logupdate);
	inittimev(Evs + TEV_PID, 0, PID_FREQ, stabilize);
	inittimev(Evs + TEV_CHECK, 0, CHECK_FREQ, checkconnection);
	inittimev(Evs + TEV_BARO,
		0 * PID_FREQ / TEV_COUNT * (TICKSPERSEC / PID_FREQ),
		DPS_FREQ, baroupdate);
	inittimev(Evs + TEV_MAG,
		1 * PID_FREQ / TEV_COUNT * (TICKSPERSEC / PID_FREQ),
		QMC_FREQ, magupdate);
	inittimev(Evs + TEV_TELE,
		2 * PID_FREQ / TEV_COUNT * (TICKSPERSEC / PID_FREQ),
		TELE_FREQ, telesend);
	inittimev(Evs + TEV_POWER,
		3 * PID_FREQ / TEV_COUNT * (TICKSPERSEC / PID_FREQ),
		POWER_FREQ, powercheck);
	inittimev(Evs + TEV_AUTOPILOT,
		4 * PID_FREQ / TEV_COUNT * (TICKSPERSEC / PID_FREQ),
		AUTOPILOT_FREQ, autopilotupdate);

	// initilize debug commands
	addcommand("r", rcmd);
	addcommand("info", infocmd);
	addcommand("flash", flashcmd);
	addcommand("system", systemcmd);
	addcommand("log", logcmd);
	addcommand("motor", motorcmd);
	addcommand("autopilot", autopilotcmd);
	addcommand("set", setcmd);
	addcommand("get", getcmd);
	addcommand("apply", applycmd);

	__HAL_TIM_SET_COUNTER(pconf_schedhtim, 0);

	Init = 1;

	// main control loop
	while (1) { }

	return 0;
}

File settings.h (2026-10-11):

/**
* @file settings.h
* @brief Settings management functions
*/

#ifndef SETTINGS_H
#define SETTINGS_H

#include "log.h"

/**
* @brief Is debug uart interactive
*/
#define INTERACTIVE_UART 0

/**
* @brief Is event profiler enabled
*/
#define PROFILER_ENABLED 1

/**
* @brief Periodic event timer ticks per second
*/
#define TICKSPERSEC 1000000

/**
* @brief Maximum length for info packet sent back to operator
*/
#define INFOLEN 512

/**
* @brief Maximum length for control command
*/
#define CMDSIZE 64

/**
* @brief MCU flash address where quadcopter settings is stored
*/
#define USER_FLASH 0x080e0000

/**
* @defgroup EVENTFREQUENCIES
* @brief Periodic events frequencies
* @{
*/

#ifdef STM32F4xx
#define PID_FREQ 4000		/*!< PID event frequency */
#elif STM32H7xx
#define PID_FREQ 8000		/*!< PID event frequency */
#endif

#define CHECK_FREQ 1		/*!< connection check event frequency */
#define DPS_FREQ 100		/*!< barometer update event frequency */
#define QMC_FREQ 100		/*!< magnetometer update event frequency */
#define TELE_FREQ 100		/*!< telemetry send event frequency */
#define POWER_FREQ 100		/*!< battery power update event frequency */
#define AUTOPILOT_FREQ 100	/*!< autopilot update event frequency */
/**
* @}
*/

/**
* @brief Timeout in seconds before quadcopter disarm
	when got no data from ERLS receiver
*/
#define ELRS_TIMEOUT 2

/**
* @brief Time required to register button push,
	used for buttons and switches that controls
	time consuming functions
*/
#define ELRS_PUSHTIMEOUT 0.1

/**
* @defgroup ERLSCHANNELS
* @brief eRLS channels mapping
* @{
*/
#define ERLS_CH_ROLL		0	/*!< roll channel */
#define ERLS_CH_PITCH		1	/*!< pitch channel */
#define ERLS_CH_THRUST		2	/*!< throttle channel */
#define ERLS_CH_YAW		3	/*!< yaw channel */
#define ERLS_CH_YAWMODE		4	/*!< yaw mode channel */
#define ERLS_CH_ATTMODE		5	/*!< attitude mode channel */
#define ERLS_CH_THRMODE		6	/*!< altitude mode channel */
#define ERLS_CH_ONOFF		7	/*!< on/off channel */
#define ERLS_CH_ALTCALIB	8	/*!< recalibration channel */
#define ERLS_CH_GNSSMODE	9	/*!< gnss hold mode channel */
#define ERLS_CH_HOVER		10	/*!< hover mode channel */
#define ERLS_CH_AUTOPILOT	11	/*!< autopilot mode channel */
#define ERLS_CH_SETSLOT		15	/*!< settings slot channel */
/**
* @}
*/

/**
* @brief Maximum autopilot track points
*/
#define MAX_POINT_COUNT 16

/**
* @defgroup DEF default settings values
* @{
*/
#define LTDEFNUM 0	/*!< left-top motor default output number */
#define LBDEFNUM 1	/*!< left-bottom motor default output number */
#define RBDEFNUM 2	/*!< right-bottom motor default output number */
#define RTDEFNUM 3	/*!< right-top motor default output number */

#define LOGDEFFREQ 128			/*!< default log frequency */
#define LOGDEFRECSIZE 4			/*!< default log size */
#define LOGFIELDDEFPOS 99		/*!< default log
					field position */
#define IRCDEFPOWER IRC_POWER_25	/*!< default video TX power */
#define IRCDEFFREQ IRC_FREQ_5733	/*!< default video
					TX frequency */
/**
* @}
*/

/**
* @brief Quadcopter setting's slot
*/
#define USER_SETSLOTS (0x80 / sizeof(struct settings))

/**
* @defgroup COMP settings that set at compile time
* @{
*/
#define PID_MAX_I 0.5		/*!< maximum PID I-term value */
#define PID_MAX_ATTS_I 0.15	/*!< maximum rotation speed PID
					I-term value */
#define PID_MAX_THR_I 0.3	/*!< maximum throttle PID I-term
					value */

#define PID_MAX_I 0.5		/*!< maximum PID I-term value */
#define BAT_CUTOFF 10.0		/*!< battery voltage sensor
				filter cut-off frequency */
#define CUR_CUTOFF 10.0		/*!< battery current sensor
				filter cut-off frequency */
#define TEMP_TCOEF 0.318	/*!< PCB temperature filter
				time coefficient */
#define VA_AVG_TCOEF 0.08	/*!< averaging low-pass filter
				time coefficient for vectical
				acceleration */
#define BAT_SCALE 28.05		/*!< battery sensor voltage scale */
/**
* @}
*/
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

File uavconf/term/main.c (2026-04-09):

#include <sys/socket.h>
#include <arpa/inet.h>
#include <fcntl.h>
#include <inttypes.h>
#include <stdarg.h>
#include <unistd.h>
#include <limits.h>
#include <libgen.h>
#include <stdio.h>
#include <errno.h>
#include <stdlib.h>
#include <string.h>

#include "../api/uavconf.h"

/**
* Log size in records
*/
#define LOGSIZE (1024 * 64)

/**
* Maximum UAV command size
*/
#define CMDMAXSZ 60

/**
* Socket send/receive buffer size
*/
#define BUFSZ 1024

/**
* @brief Handle command got from terminal.
* @param event key press event
* @param lsfd UDP socket for configuration connection
* @param rsi quadcopter's esp8285 IP address
* @return 1, if exit command was read, 0 otherwise
*/
int handlecmd(const char *cmd, int lsfd, const struct sockaddr_in *rsi)
{
	char buf[CMDMAXSZ];

	// if got one of known commands, perform corresponding actions.
	// In other case just send it into UDP socket.
	if (strcmp(cmd, "e") == 0)
		return 1;
	else if (strcmp(cmd, "m") == 0)
		sendcmd(lsfd, rsi, "info mpu\n", NULL, NULL, NULL);
	else if (strcmp(cmd, "p") == 0)
		sendcmd(lsfd, rsi, "info pid\n", NULL, NULL, NULL);
	else if (strcmp(cmd, "v") == 0)
		sendcmd(lsfd, rsi, "info values\n", NULL, NULL, NULL);
	else if (strcmp(cmd, "h") == 0)
		sendcmd(lsfd, rsi, "info qmc\n", NULL, NULL, NULL);
	else if (strcmp(cmd, "b") == 0)
		sendcmd(lsfd, rsi, "info hp\n", NULL, NULL, NULL);
	else if (strcmp(cmd, "g") == 0)
		sendcmd(lsfd, rsi, "info gnss\n", NULL, NULL, NULL);
	else if (strcmp(cmd, "d") == 0)
		sendcmd(lsfd, rsi, "info dev\n", NULL, NULL, NULL);
	else if (strcmp(cmd, "t") == 0)
		sendcmd(lsfd, rsi, "info ctrl\n", NULL, NULL, NULL);
	else if (strcmp(cmd, "f") == 0)
		sendcmd(lsfd, rsi, "info filter\n", NULL, NULL, NULL);
	else if (strcmp(cmd, "i") == 0)
		sendcmd(lsfd, rsi, "info irc\n", NULL, NULL, NULL);
	else if (strcmp(cmd, "w") == 0) {
		sprintf(buf, "log set %d\n", LOGSIZE);
		sendcmd(lsfd, rsi, buf, NULL, NULL, NULL);
	}
	else if (strcmp(cmd, "s") == 0)
		sendcmd(lsfd, rsi, "log set 0\n", NULL, NULL, NULL);
	else if (strcmp(cmd, "r") == 0) {
		char *output;
		size_t outsize;

		getlog(lsfd, rsi, 0, LOGSIZE, &output, &outsize,
			NULL, NULL);

		printf("%s", output);
	}
	else if (strcmp(cmd, "c") == 0)
		sendcmd(lsfd, rsi, "c 0.0\n", NULL, NULL, NULL);
	else {
		sprintf(buf, "%s\n", cmd);
		sendcmd(lsfd, rsi, buf, NULL, NULL, NULL);
	}

	return 0;
}

/**
* @brief Entry point.
* @param argc command line agruments count
* @param argv command line arguments 
* return always 0
*/
int main(int argc, char *argv[])
{
	struct sockaddr_in rsi;
	char *buf;
	size_t bufsz;
	int lsfd;

	// initilize connection sockets
	initsocks(&lsfd, &rsi);

	// if has a command line argument, apply configuration file
	if (argc > 1) {
		FILE *f;
		char s[CMDMAXSZ];

		// open configuration file
		if ((f = fopen(argv[1], "r")) == NULL) {
			fprintf(stderr, "cannot open file %s\n",
				argv[1]);
			exit(1);
		}

		// read opened file line-by-line sending
		// every line as a configuration command
		while (fgets(s, CMDMAXSZ, f) != NULL)
			sendcmd(lsfd, &rsi, s, conffunc, NULL, NULL);
	}

	// poll for standant input and UDP socket for incoming data.
	buf = NULL;
	bufsz = 0;
	while (1) {
		fd_set rfds;

		// use select for input multiplexing
		FD_ZERO(&rfds);
		FD_SET(0, &rfds);
		FD_SET(lsfd, &rfds);

		if (select(lsfd + 1, &rfds, NULL, NULL, NULL) <= 0)
			continue;

		// if got data on standart input, read
		// one line and interpret it as command
		if (FD_ISSET(0, &rfds)) {
			ssize_t l;
			l = getline(&buf, &bufsz, stdin);

			if (buf[l - 1] == '\n')
				buf[l - 1] = '\0';

			if (handlecmd(buf, lsfd, &rsi) != 0)
				break;
		}

		// uf got data on UDP socket, print
		// it to standart output.
		if (FD_ISSET(lsfd, &rfds)) {
			char buf[BUFSZ + 1];
			socklen_t rsis;
			int rsz;

			rsis = sizeof(rsi);
			if ((rsz = recvfrom(lsfd, buf, BUFSZ, 0,
				(struct sockaddr *) &rsi, &rsis)) > 0) {
				buf[rsz] = '\0';
				printf("%s", buf);
			}
		}
	}

	// free buffer used by getline
	free(buf);

	return 0;
}

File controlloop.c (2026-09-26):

#include <math.h>

#include "controlloop.h"
#include "runvals.h"
#include "settings.h"
#include "periphconf.h"

#include "device.h"
#include "icm42688.h"
#include "dps368.h"
#include "esp8266.h"
#include "qmc5883l.h"
#include "crsf.h"
#include "w25.h"
#include "m10.h"
#include "uartconf.h"
#include "irc.h"
#include "msp.h"
#include "dshot.h"

/**
* @brief Calculate tilt compensated heading direction
	using magnetometer readings, roll value and pitch value.
* @param r roll value
* @param p pitch value
* @param x magnetometer's X axis value
* @param y magnetometer's Y axis value
* @param z magnetometer's Z axis value
* @return tilt compensated heading
*/
static double heading(double r, double p, double x, double y, double z)
{
	x = x * cos(p) + y * sin(r) * sin(p)
		+ z * cos(r) * sin(p);
	y = y * cos(r) - z * sin(r);

	return circf(atan2(y, x) + St.adj.magdecl);
}

int setstabilize(int init)
{
	double iscale;

	// init complementary filters contexts
	dsp_setcompl(Cmpl + CMPL_PITCH, St.cmpl.att, PID_FREQ, init);
	dsp_setcompl(Cmpl + CMPL_ROLL, St.cmpl.att, PID_FREQ, init);

	dsp_setcomplv2(&Cmplv, St.cmpl.att, PID_FREQ, init);

	dsp_setcompl(Cmpl + CMPL_YAW, St.cmpl.yaw, PID_FREQ, init);

	dsp_setcompl(Cmpl + CMPL_CLIMBRATE, St.cmpl.climbrate,
		PID_FREQ, init);
	dsp_setcompl(Cmpl + CMPL_ALT, St.cmpl.alt, PID_FREQ, init);

	dsp_setcompl(Cmpl + CMPL_LCLIMBRATE, St.cmpl.lclimbrate,
		PID_FREQ, init);
	dsp_setcompl(Cmpl + CMPL_GNDALT, St.cmpl.gndalt,
		PID_FREQ, init);

	dsp_setcompl(Cmpl + CMPL_SLAT, St.cmpl.speed, PID_FREQ, init);
	dsp_setcompl(Cmpl + CMPL_SLON, St.cmpl.speed, PID_FREQ, init);
	dsp_setcompl(Cmpl + CMPL_LAT, St.cmpl.pos, PID_FREQ, init);
	dsp_setcompl(Cmpl + CMPL_LON, St.cmpl.pos, PID_FREQ, init);

	// init roll and pitch position PID controller contexts
	dsp_setpidbl(Pid + PID_PITCHP,
		St.pid.attpos.p, St.pid.attpos.i, St.pid.attpos.d,
		PID_MAX_I, St.lpf.d, 0, PID_FREQ, init);
	dsp_setpidbl(Pid + PID_ROLLP,
		St.pid.attpos.p, St.pid.attpos.i, St.pid.attpos.d,
		PID_MAX_I, St.lpf.d, 0, PID_FREQ, init);

	// init roll, pitch and yaw speed PID controller contexts
	iscale = Speedpid ? 1.0 : St.pid.feature.iscale;
	
	dsp_setpidbl(Pid + PID_PITCHS,
		St.pid.attrate.p,
		St.pid.attrate.i * iscale,
		St.pid.attrate.d,
		St.pid.feature.attimax, St.lpf.d, 0, PID_FREQ, init);
	dsp_setpidbl(Pid + PID_ROLLS, 
		St.pid.attrate.p,
		St.pid.attrate.i * iscale,
		St.pid.attrate.d,
		St.pid.feature.attimax, St.lpf.d, 0, PID_FREQ, init);
	dsp_setpidbl(Pid + PID_YAWS,
		St.pid.yawrate.p,
		St.pid.yawrate.i * iscale,
		St.pid.yawrate.d,
		St.pid.feature.attimax, St.lpf.d, 0, PID_FREQ, init);

	// init yaw position PID controller's context
	dsp_setpidbl(Pid + PID_YAWP,
		St.pid.yawpos.p, St.pid.yawpos.i, St.pid.yawpos.d,
		PID_MAX_I, St.lpf.d, 1, PID_FREQ, init);

	// init vertical acceleration PID controller's context
	dsp_setpidbl(Pid + PID_VA,
		St.pid.throttle.p, St.pid.throttle.i, St.pid.throttle.d,
		St.pid.feature.thrimax, St.lpf.d, 0, PID_FREQ, init);

	// init climbrate PID controller's context
	dsp_setpidbl(Pid + PID_CLIMBRATE,
		St.pid.climbrate.p, St.pid.climbrate.i,
		St.pid.climbrate.d, PID_MAX_I, St.lpf.d, 0, PID_FREQ,
		init);

	// init altitude PID controller's context
	dsp_setpidbl(Pid + PID_ALT,
		St.pid.alt.p, St.pid.alt.i, St.pid.alt.d,
		PID_MAX_I, St.lpf.d, 0, PID_FREQ, init);

	// init speed through latitude and longitude 
	// PID controllers contexts
	dsp_setpidbl(Pid + PID_SLAT,
		St.pid.speed.p, St.pid.speed.i, St.pid.speed.d,
		PID_MAX_I, St.lpf.d, 0, PID_FREQ, init);

	dsp_setpidbl(Pid + PID_SLON,
		St.pid.speed.p, St.pid.speed.i, St.pid.speed.d,
		PID_MAX_I, St.lpf.d, 0, PID_FREQ, init);

	// init latitude and longitude PID controllers contexts
	dsp_setpidbl(Pid + PID_LAT,
		St.pid.pos.p, St.pid.pos.i, St.pid.pos.d,
		PID_MAX_I, St.lpf.d, 0, PID_FREQ, init);

	dsp_setpidbl(Pid + PID_LON,
		St.pid.pos.p, St.pid.pos.i, St.pid.pos.d,
		PID_MAX_I, St.lpf.d, 0, PID_FREQ, init);

	// init battery voltage low-pass filter
	dsp_setlpf1f(Lpf + LPF_BAT, BAT_CUTOFF, POWER_FREQ, init);
	dsp_setlpf1f(Lpf + LPF_CUR, CUR_CUTOFF, POWER_FREQ, init);

	// init average thrust low-pass filter
	dsp_setunity(Lpf + LPF_AVGTHR, init);
	dsp_setlpf1f(Lpf + LPF_AVGTHRA, St.lpf.va, PID_FREQ, init);

	// init low-pass fitlers for altitude, accelerations and speed
	dsp_setunity(Lpf + LPF_BARTEMP, init);
	dsp_setlpf1f(Lpf + LPF_THR, St.lpf.va, PID_FREQ, init);
	dsp_setunity(Lpf + LPF_VAU, init);
	dsp_setlpf1f(Lpf + LPF_VAPT1, St.lpf.va, PID_FREQ, init);
	dsp_setlpf1f(Lpf + LPF_VAAVG, VA_AVG_TCOEF, PID_FREQ, init);
	dsp_setunity(Lpf + LPF_FA, init);
	dsp_setunity(Lpf + LPF_SA, init);
	dsp_setunity(Lpf + LPF_ALT, init);
	dsp_setunity(Lpf + LPF_SPEED, init);
	dsp_setunity(Lpf + LPF_LATM, init);
	dsp_setunity(Lpf + LPF_LONM, init);
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

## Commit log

2024-05-26 trying to fix accelerometer and gyro noise with woking motors
    [main.c, mpu6500.c]
2024-05-27 Trying to stabilize at high throttle; bgp280 added
    [bmp280.c, main.c, mpu6500.c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]
2024-05-27 experimenting with PWM frequency
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2024-05-30 Trying to adjust PID and accelerometer
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2024-07-23 complementary filter time constant settting command added, README updated
2024-08-11 Readme changed, battery is now 2s, swithced to oneshot125
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2024-08-15 lpf fixed, experimenting with altitude stabilization by pressure
    [main.c]
2024-08-18 trying to make magnetometer work
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2024-08-28 Swithced to simpler MCU, README.txt updated, magnetometer calibration mode added
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2024-08-28 ADC readings fixed, cosmetic main loop changes, barometer readings moved from main PID loop
    [main.c]
2024-08-28 magnetic declination moved into settaings, device drivers moved to separate directory
2024-08-28 timer event callbacks added
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2024-09-15 trying to find errors
    [crsf.c, esp8266.c, main.c]
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2024-10-11 Trying to add error check to elrs
    [crsf.c, main.c]
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2024-10-14 trying to fix magnitometer pid loop
    [esp8266.c, main.c]
2024-10-15 trying to fix magnetometer
    [main.c]
2024-10-15 yaw loop return commented lines
2024-10-29 switched to a new board
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2024-10-30 dc-dc circuit fix
2024-11-08 magnetometer reading moved to separate event, i2c digital filter disabled
2024-11-14 yaw control is now performed by left joystick
2024-11-24 altitude reset from elrs
    [hp206c.c, main.c]
2024-11-24 arming indication and error leds added
    [main.c]
2024-11-26 trying to estimate climb rate from accelerometer
2024-12-03 yaw mode switch added
2024-12-05 gyro calibration on start removed
2024-12-23 switched to new board, with mpu6500
2025-02-25 Tried to fix baudrate on-run change for esp8266, removed hardcoded mpu6500 offsets
    [esp8266.c, main.c, mpu6500.c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]
2025-02-25 SPI baudrate divider set to 4, some cleanup
2025-02-25 flash log fixes, log set size commands added
    [main.c, w25.c]
2025-02-26 gyroscope and magnetometer calibration
2025-02-26 event timer remain added
2025-02-27 fixed w25q timeouts, esp8266 baudrate slowed
    [esp8266.c, main.c, w25.c]
2025-03-08 ESP8266 switched to same interface as other devices
2025-03-09 Device status command added
2025-03-09 Telemetry fixes and refactoring
    [crsf.c, main.c]
2025-03-17 altitude complimentary filter added
2025-03-22 Yaw complimentary filter added to merge magnetometer heading and gyro z axis
2025-03-23 Motor thrust adjust added
2025-04-08 Switched to stm32f405 and ICM42688
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2025-04-17 esc pwm set to 4 kHz, control scaling setting added
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2025-05-05 switched to new board with esp connected through SPI
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2025-05-08 switched to all-in-one esc, pid frequency set to 4k
2025-05-09 pitch correction removed
2025-05-14 Fixing wifi connection for high speed upload
    [esp8266.c, icm42688.c, main.c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]
2025-05-15 Reworking confuration commands protocol
    [main.c]
2025-05-16 trying to speed up spi
2025-05-18 trying to get better spi transmition speed
2025-05-21 maximum thrust value added
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2025-05-22 emergency disarm when upside down, ESP SPI CRC check disabled
2025-05-23 disabled magnetometer check, values adjusted
2025-05-23 switched to CRC-16 for controll comamnds and log records, stm32 periphery initialization moved to separate file
2025-05-24 trying to fix accelerometer noise
    [icm42688.c, main.c]
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2025-05-24 trying to fix drifting
    [icm42688.c]
2025-05-29 esp8266 bugfixes, acro mode returned
    [esp8266.c, main.c]
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2025-06-03 IRC tramp device added
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2025-06-09 battery monitoring divider changed, battery monitor lpf added
2025-06-17 uav command check fixed
    [main.c]
2025-06-24 uavconf directory structure reworking
    [main.c]
2025-06-28 frame changed, crsf channels enum added
    [frame.dxf]
2025-06-29 Multiple setting slot enabled, 6 position switch used
2025-07-09 motor direction change reworked, some dshot cosmetic code changes, trying to fix a hard fault on startup
    [main.c]
2025-07-10 partial setting send added, trying to altitude hold make stabilize when moving
    [main.c]
2025-07-13 PID tuning for 2s battery set using Ziegler-Nichols method, I-term computing disabled disarmed
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2025-07-27 log field mapping fixes
    [irc.c, main.c]
2025-07-31 log writing fix for maximum records count, w25 timeouts bugfix, stm32 systick to float seconds utility function added
    [main.c, w25.c]
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2025-09-08 switching to dps368, working on stable altitude hold
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2025-09-12 stabilized around hover throttle acceleration mode added, altitude hold around hover throttle added
    [main.c]
2025-09-14 hover throttle tilt compensation fixed
    [main.c]
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2025-09-30 i term accumulating fixed, 4s pid adjusted
    [main.c]
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2025-11-06 i2c and uart tx processed through DMA, bilinear PID implementaion added
2025-11-06 trying to switch to bilinear transform derived PID
2025-11-07 bilinear PID implementation used, I part disabling removed
2025-11-08 bilinear transform derived PID I-term clamp and I-term reset added
    [main.c]
2025-11-10 doxugen added for settings, stm32periph, timev and util
2025-11-10 logging event enabled, set_pid return codes fixed
    [main.c]
2025-12-15 accelerometer temperature compensation setting added, magnetometer hardcoded throttle compensation added
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2025-12-18 error accumulation when disarmed is fixed
    [main.c]
2026-01-03 uart dma error fiexed, working on autopilot
    [config.c, crsf.c, main.c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]
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2026-01-12 PCB added
    [CAMtastic1_3.PcbDoc, PCB_Project.PrjPcb, PcbLib1.PcbLib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]
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2026-01-13 global variable names now start with capital letters, magnetometer offset applied immideately
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2026-01-14 roll, pitch, yaw offsets now calculated once, circular PID how using bilinear transform
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2026-02-09 device pin and interface configuration added to config
2026-02-15 devices initialization reworked
2026-02-16 makefile reworked, stm32h7 hal added
    [bmp280.c, crsf.c, dps368.c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]
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2026-02-20 fixing adc for H7
    [main.c]
2026-02-21 debug uart interrupt fixed
    [main.c, util.c]
2026-02-23 H7 schematic added, README.md updated
    [CAMtastic1_3.PcbDoc, CAMtastic1_5.PcbDoc, PCB_Project.PrjPcb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]
2026-02-24 Kicad project added for H7
    [CAMtastic1_5.PcbDoc, PCB_Project.PrjPcb, PcbLib1.PcbLib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]
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2026-02-24 schematic source updated
    [esp8285.kicad_sch, project.kicad_sch]
2026-02-24 pcb update
    [pcb.kicad_pcb]
2026-02-24 F4 pcb updated
    [CAMtastic1_3.PcbDoc, PCB_Project.PrjPcb, PcbLib1.PcbLib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]
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2026-02-25 schematic fix
    [esp8285.kicad_sch]
2026-02-26 trying to fix dshot issue with high frequency timer, schematic numbers fix
    [esp8285.kicad_sch, project.kicad_sch]
2026-03-07 esp8266 spi fix
    [esp8285.kicad_sch, project.kicad_sch]
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2026-03-07 irc vtx inittialization fix
    [config.c, irc.c, main.c]
2026-03-09 current sence fix
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2026-03-10 battery sensor scaling added, i term scaling for dual loop pid mode added, configs updated
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2026-03-10 gyro z direction fix, adc lpf cut-off changed
    [main.c, runvals.h, settings.h]
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2026-03-11 STM32F4 scheduler fix
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2026-03-19 altitude complimentary filter update moved to main PID event
2026-03-20 dshot bit length from timer frequency calculation added, tilt compensation for altitude hold added
2026-03-23 dma burst mode for dshot added, adc oversampling enabled
2026-03-25 spi frequency raised to 24 mhz for H7, maximum log frequency raised to 8khz, accelerometer range raised to 16g, adjustments changed in config, dshot-600 adjustments added
2026-03-25 dshot-600 pulse length and frequency fixes
    [dshot.c]
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2026-03-30 OSD fixes, tried to recalibrate magnetometer for digital vtx
    [msp.c, util.c]
2026-03-31 float to string fixes
    [util.c]
2026-04-02 stm32f405 adc dma enabled, stm32h7 current meter adjustments
2026-04-02 stm32f405 I2C changed to DMA+IT calls, stm32H7 deinitialization changes
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2026-04-05 osd and gps fixes
    [m10.c, msp.c]
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2026-04-07 complie error fixes, zero fill for ftos added
    [msp.c, util.c]
2026-04-08 various fixes, removing unused variables, names and types fixes, uptime added into MSP OSD, magnetic direction OSD fix
    [mpu6500.h, msp.c]
2026-04-09 doxygen updated, most constants moved to settings.h, device initializaiton struct type in init functions updated
2026-04-09 disabling magnetometer using modes and barometer using modes when corresponding sensor disabled
2026-04-10 event triggering now bound to PID frequency, accelerometer reading moved to separate event, log writing batch size changed to 128 bytes, trying to fix wifi log downloading
    [esp8266.c, log.h, main.c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]
2026-04-12 overrun error handling added for SPI receive function, debug version of firmware added
    [esp8266.c, w25.c]
2026-04-14 empty command crc check fix, gui downloaded size output added, gnss log fields added
    [command.c, log.h, main.c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]
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2026-04-17 barometric altitude speed correction added
    [config.c, main.c, runvals.h]
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2026-04-20 accelerometer euler angles and rotation matrix fix
    [config.c, main.c]
2026-04-21 gyro calibration added, attitude complimentary filter time constant adjusted
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2026-04-30 camera holder cad file added
    [cameraholder.FCStd]
2026-05-02 gnss speed control fix
    [main.c]
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2026-05-15 PCB and CAD files updated
    [cameraholder.FCStd, canopy.FCStd, dcdc.kicad_pcb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]
2026-05-25 swtiched to mmc5983ma
    [mmc5983ma.kicad_pcb]
2026-05-27 canopy holes sizes updated, 2S PIDs updated
    [canopy.FCStd]
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2026-06-06 canopy updated
    [canopy.FCStd]
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2026-06-10 switched to new board with imu and w25q on separate SPIs
    [pcb.kicad_pcb]
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2026-06-18 trying to fix I-term accumulation
    [config.c, controlloop.c, settings.h]
2026-06-20 thrust linearilation fix
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2026-06-23 log flash double buffering added, trying to fix dps368 data reading
    [dps368.c, settings.h, w25.c]
